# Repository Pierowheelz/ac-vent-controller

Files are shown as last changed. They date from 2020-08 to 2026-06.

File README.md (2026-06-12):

# Ducted Air Conditioner Vent Controller
This project uses an ESP32-based controller, stepper motors, TMC2209 (or similar) drivers and endstop switches (from a 3d printer kit) to control the circular Air Conditioner vents used in many ducted HVAC systems.
Each board can control up to 4 vents (leave the stepper header empty and tweak the /AC_Vent/config.h to control fewer vents). Multiple boards can be utilised to control more vents, or for vents too far from one board.

# Home Automation
This project is part of a larger ecosystem, designed to enable automation of vents based on the room temperatures, along with an App for manual control.
* [home-app-backend](https://github.com/Pierowheelz/home-app-backend) - backend API and automation logic
* [home-control](https://github.com/Pierowheelz/home-control) - web app for manual control

## Parts Required
* ESP32 Dev Board (NodeMCU-ESP32 DEVKITV1 - 30 pins - based on ESP-WROOM-32)
* 3D Printer Kit (from ebay or Aliexpress)
    * 4x Nema 17 stepper motors + cables
    * 4x Nema 17 mounting brackets
    * 4x Stepper motors drivers - A4988 or DRV8825 or TMC2208 (for quieter operation)
    * 4x RAMPS 1.4 switch endstops + cables (Note, swap the trigger switch for a waterproof one for more reliable operation, but keep the switch PCB)
* Order the PCB from the Gerber files (or custom-build with Perfboard 24 x 18 pins)
* 4x 150mm Lead screws + copper nuts (4mm pitch ideal, but any will work)
* DC-DC Buck convertor TRS2433 (or you can use an LM2596 set to 3.3v if DIYing the board)
* DC power supply (8-35 V)
* (optional) header-pin sockets for ESP32 and Stepper Drivers to allow quick removal/replacement
* A handfull of M4 screws & nuts
* Duct tape

## Process
1. Order the custom PCM from the Gerber files in the Circuit Board V2/ directory.
1. Print 4x Motor Bracket, Motor Cover, Endstop Clip in PLA or PETG (or other hard-plastic).
1. Print 4x Coupler, Damper and 8x End Holder in TPU (for vibration damping - PLA will work in a pinch though). Metal couplers from a 3d printer kit can also be used.
1. Assemble the circuitboard per the KiCad schematic or using the silk screen guides.
1. Set the ventNames, microStepping, WiFi parameters in the firmware (see AC_Vent/README_CONFIG.md for details).
1. Compile and flash the firmware onto your ESP32 dev board using Arduino IDE.
    * Using USB for power (do not plug in the power supply for this).
    * NOTE: Setup Arduino IDE with ESP32 library like this: https://randomnerdtutorials.com/installing-the-esp32-board-in-arduino-ide-windows-instructions/
1. Bench test by connecting motors and endstop switches.
    * You may need to switch the red and black wires on your endstop switches (black should be at the edge of the board, and red in the middle).
1. Connect the power supply to the high-voltage side of the buck convertor. This will power up the ESP32.
1. Tune the stepper motor current limit (Try this guide: https://www.makerguides.com/a4988-stepper-motor-driver-arduino-tutorial/).
    * Using USB for power (do not plug in the power supply for this).
1. On a computer, navigate to the IP Address of the device.
1. Click to open one of the Vents.
    * It will first spin counter-clockwise to close the vent until the endstop switch is triggered, then clockwise until the limit position is reached.
	* Note: If the motor spins the wrong direction, simply unplug and reverse it's connector.
1. Assemble components and install into vents. Tip: use Ethernet cable to extend leads as neccessary (I used RJ45 breakout modules but you could crimp connectors).

Note: There is no security or authentication in this system. Do not open up the port in your Router! For use on your internal network only.

## Usage via Rest API
Get vents status: `GET http://192.168.2.110/?&t=1`

Sample return:
```
{
	"0": {
		"name": "Room #1",
		"pos": 30
	},
	"1": {
		"name": "Room #2",
		"pos": 60
	},
	"2": {
		"name": "Room #3",
		"pos": 100
	}
}
```

Open vent `#1` to 100%: `GET http://192.168.2.110/?a=6&t=1&m=0&d=100`
Here `a` is the operating mode, where mode 6 corresponds to: open to ratio set by &d= (eg. ?d=050:open50%, ?d=000:close, ?d=100:open100%).
Also, `t` is the response type (1 = JSON).
And, `m` is the motor number (0-2).

The return format is identical to the 'get status' request.

## Images
Note: Some photos are from the prototype.

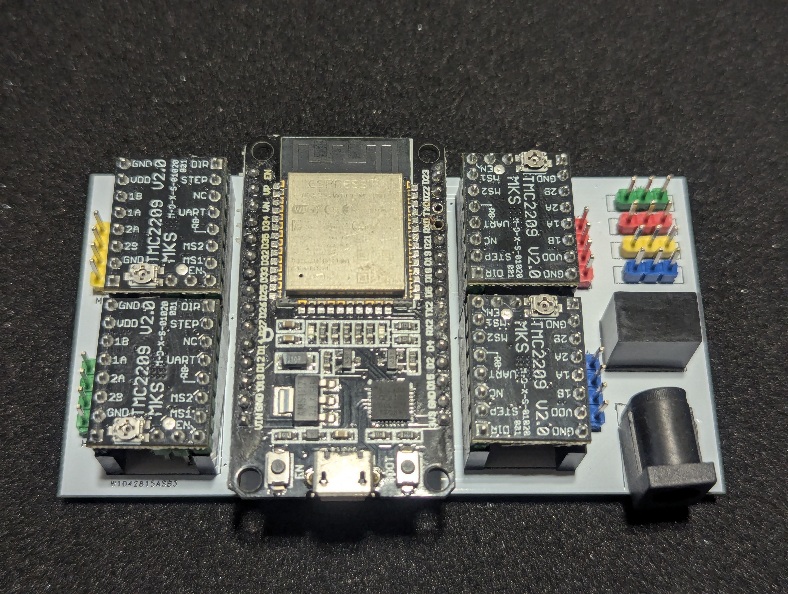
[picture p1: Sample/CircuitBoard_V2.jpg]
CircuitBoard_V2


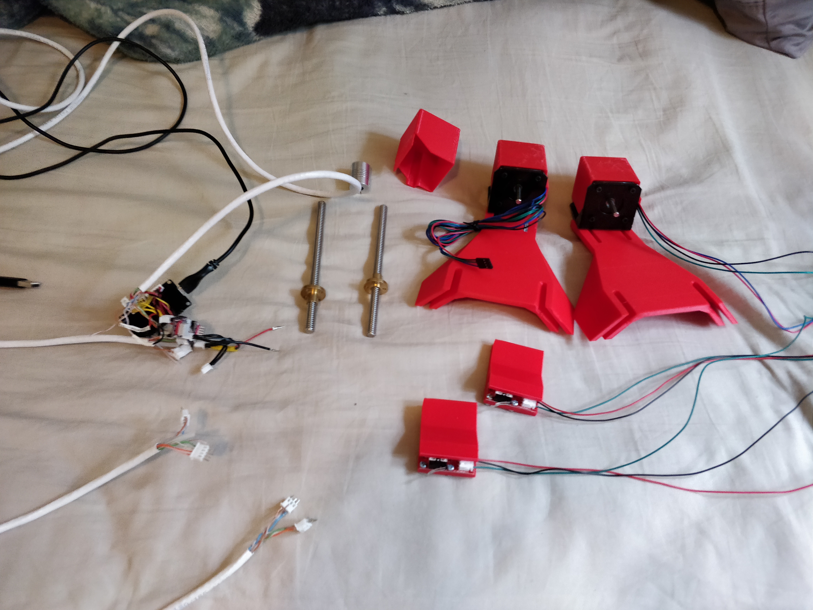
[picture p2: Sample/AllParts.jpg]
AllParts


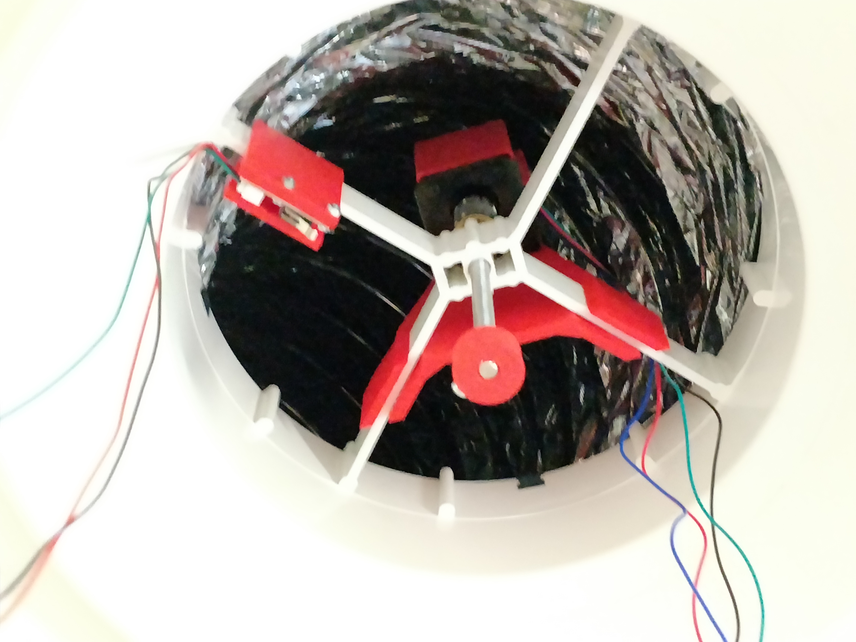
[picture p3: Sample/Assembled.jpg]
Assembled


BoartTop

BoardRear

BoardAssembled

BoardAssembled2

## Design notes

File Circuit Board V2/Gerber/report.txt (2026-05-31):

Plotted to '/home/peter/Apps/ac-vent-controller/Circuit Board V2/Gerber/Circuit Board V2-F_Cu.gtl'.
Plotted to '/home/peter/Apps/ac-vent-controller/Circuit Board V2/Gerber/Circuit Board V2-B_Cu.gbl'.
Plotted to '/home/peter/Apps/ac-vent-controller/Circuit Board V2/Gerber/Circuit Board V2-F_Paste.gtp'.
Plotted to '/home/peter/Apps/ac-vent-controller/Circuit Board V2/Gerber/Circuit Board V2-B_Paste.gbp'.
Plotted to '/home/peter/Apps/ac-vent-controller/Circuit Board V2/Gerber/Circuit Board V2-F_Silkscreen.gto'.
Plotted to '/home/peter/Apps/ac-vent-controller/Circuit Board V2/Gerber/Circuit Board V2-B_Silkscreen.gbo'.
Plotted to '/home/peter/Apps/ac-vent-controller/Circuit Board V2/Gerber/Circuit Board V2-F_Mask.gts'.
Plotted to '/home/peter/Apps/ac-vent-controller/Circuit Board V2/Gerber/Circuit Board V2-B_Mask.gbs'.
Plotted to '/home/peter/Apps/ac-vent-controller/Circuit Board V2/Gerber/Circuit Board V2-Edge_Cuts.gm1'.
Info: Done.

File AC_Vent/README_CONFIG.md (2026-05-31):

# AC Vent Controller Configuration

This project uses a separate configuration file to keep sensitive information out of version control.

## Setup Instructions

1. **Copy the sample configuration:**
   ```bash
   cp config_sample.h config.h
   ```

2. **Edit `config.h` with your actual values:**
   - WiFi SSID and password
   - Room names
   - IP addresses
   - Pin assignments (if different from default)
   - Motor settings

3. **Upload to your ESP32 as usual**

## Important Security Notes

- **`config.h` is ignored by git** and contains sensitive information
- **Never commit `config.h`** to version control
- **`config_sample.h`** is a template that can be committed safely
- Share `config_sample.h` with others but keep your `config.h` private

## Configuration Variables

- `NUM_MOTORS`: Number of vent motors (default: 4)
- `dirPins[]`: Direction control pins for each motor
- `stepper[]`: Step control pins for each motor
- `stepperPower[]`: Power control pins for each motor
- `endStop[]`: Endstop sensor pins for each motor
- `ventNames[]`: Display names for each vent/room
- `microStepping`: Microstepping setting (default: 8)
- `fullyOpen`: Steps for full vent opening (default: 1000)
- `stepDelay`: Delay between steps in microseconds (default: 2000)
- WiFi settings: SSID, password, and IP configuration

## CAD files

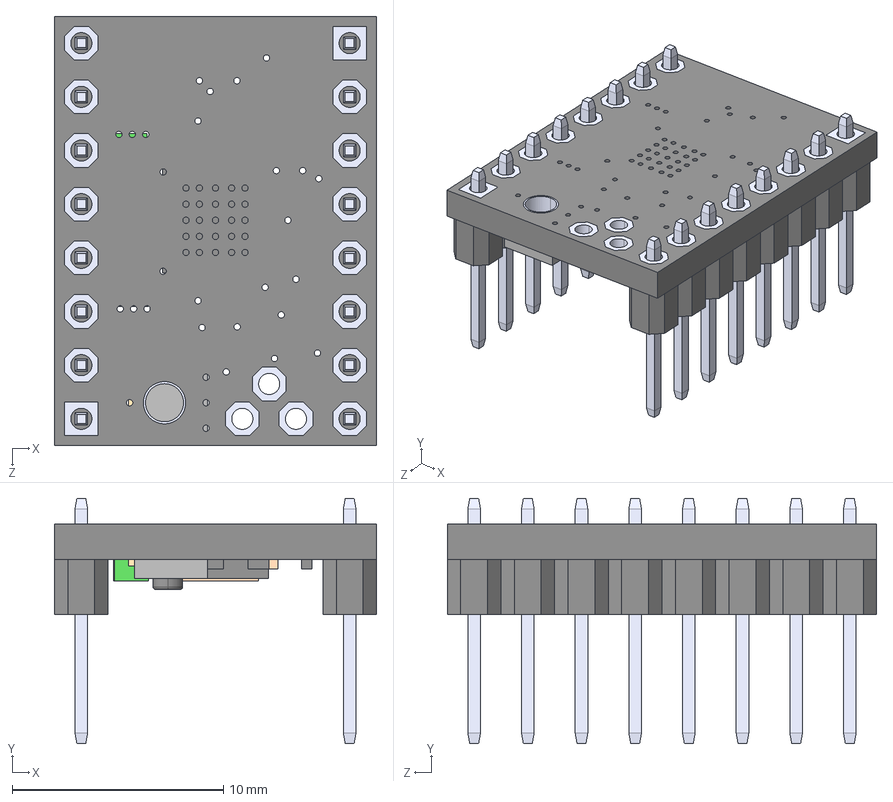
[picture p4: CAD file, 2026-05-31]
Circuit Board V2/ESP32/TMC2209_SILENTSTEPSTICK.step
15.2 x 11.6 x 20.3 mm

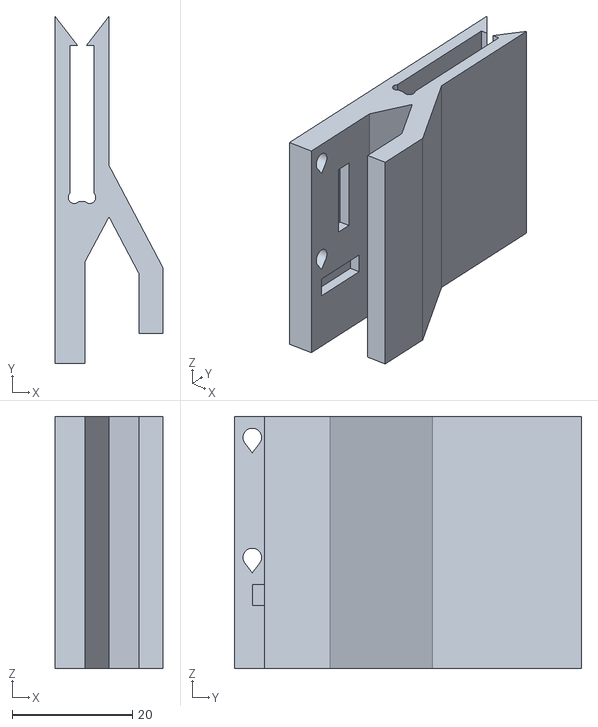
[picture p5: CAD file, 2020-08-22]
Parts/endstop-clip.stl
18.0 x 57.9 x 42.0

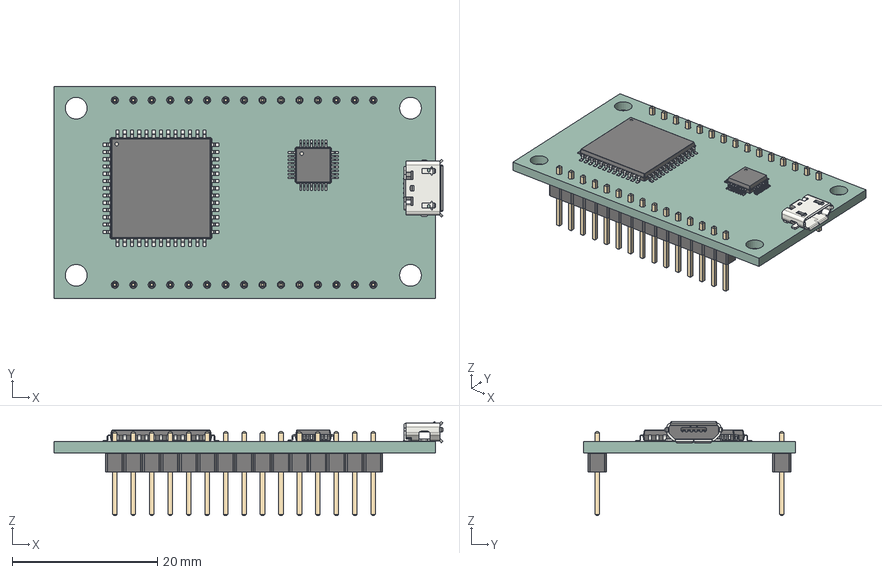
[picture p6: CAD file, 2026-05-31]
Circuit Board V2/ESP32/ESP32-30pin.step
53.5 x 29.2 x 12.9 mm
LQFP_52_14x14mm_P1mm
USB_Micro-B_Molex_47346-0001
LQFP_32_5x5mm_P05mm
PinHeader_1x15_P254mm_Vertical x 2
ESP32-30pin PCB

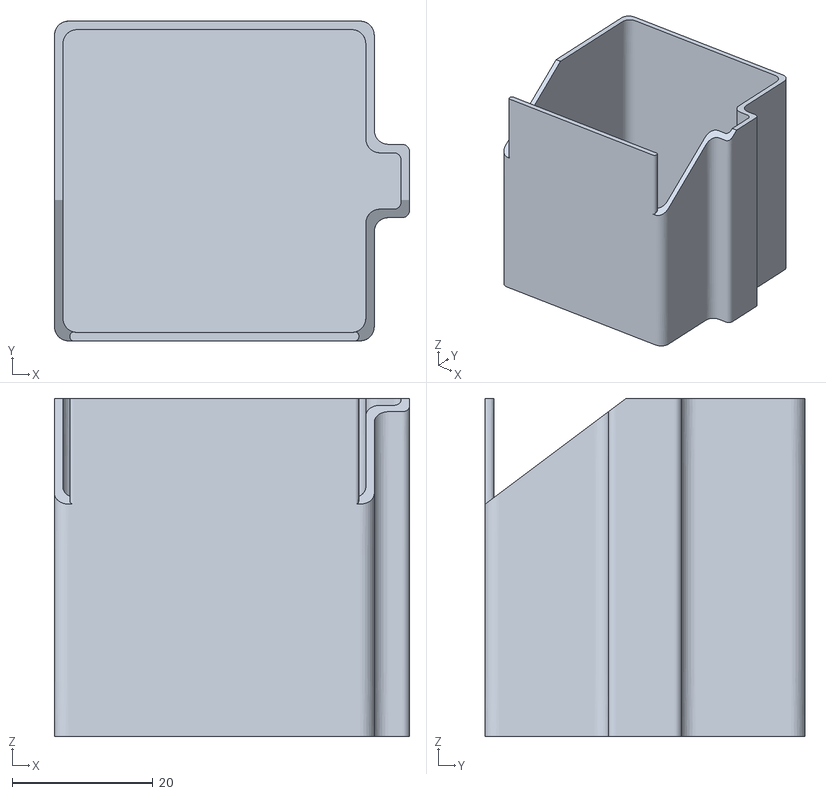
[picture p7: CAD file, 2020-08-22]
Parts/motor-cover.stl
50.4 x 45.4 x 48.0

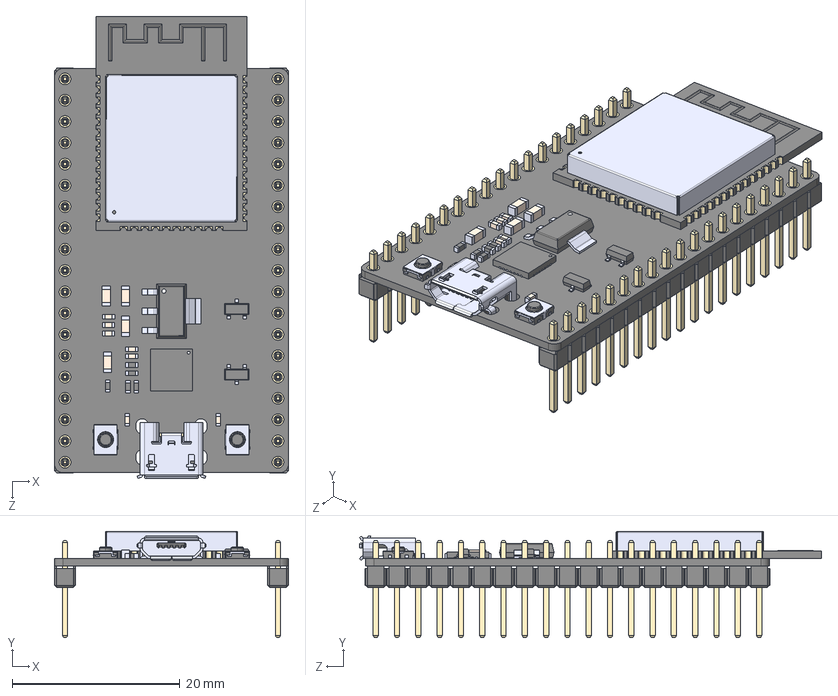
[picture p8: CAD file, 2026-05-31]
Circuit Board V2/ESP32/DEVKIT_V1_ESP32-WROOM-32.step
27.9 x 12.7 x 55.1 mm
board
header x 2
ESP32-WROOM-32D
micro usb
button x 2
CP2102N-A01-GQFN28
AMS1117-3.3
SS8050-G
components^DEVKIT V1 ESP32-WROOM-32

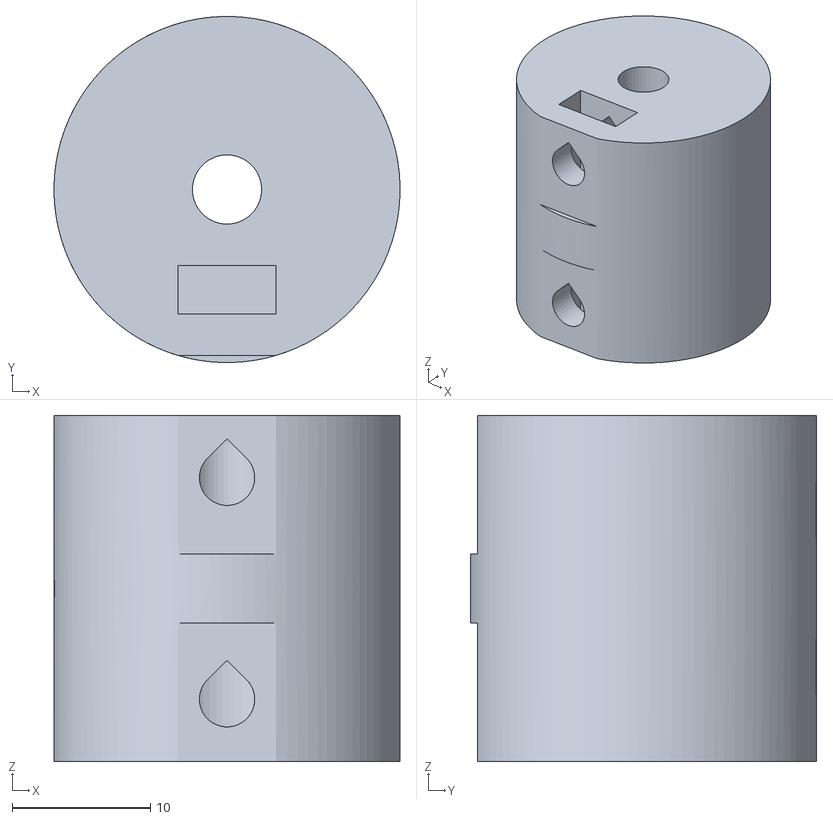
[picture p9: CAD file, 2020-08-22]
Parts/coupler.stl
25.0 x 25.0 x 25.0

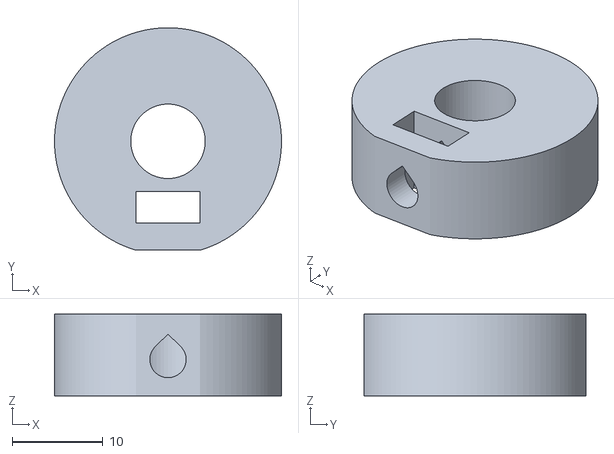
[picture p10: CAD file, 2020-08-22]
Parts/end-holder.stl
25.0 x 24.5 x 9.00

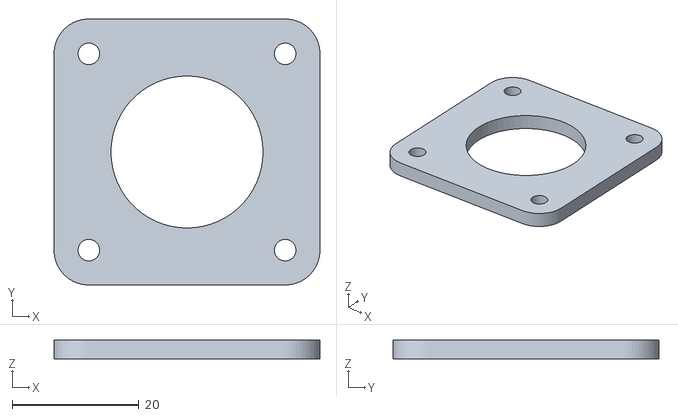
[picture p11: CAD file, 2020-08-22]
Parts/damper.stl
42.0 x 42.0 x 3.00

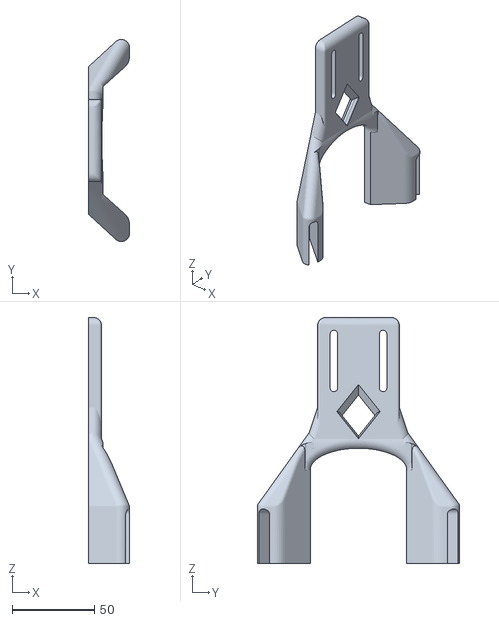
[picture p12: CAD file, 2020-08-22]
Parts/motor-bracket.stl
25.0 x 123.2 x 150.0

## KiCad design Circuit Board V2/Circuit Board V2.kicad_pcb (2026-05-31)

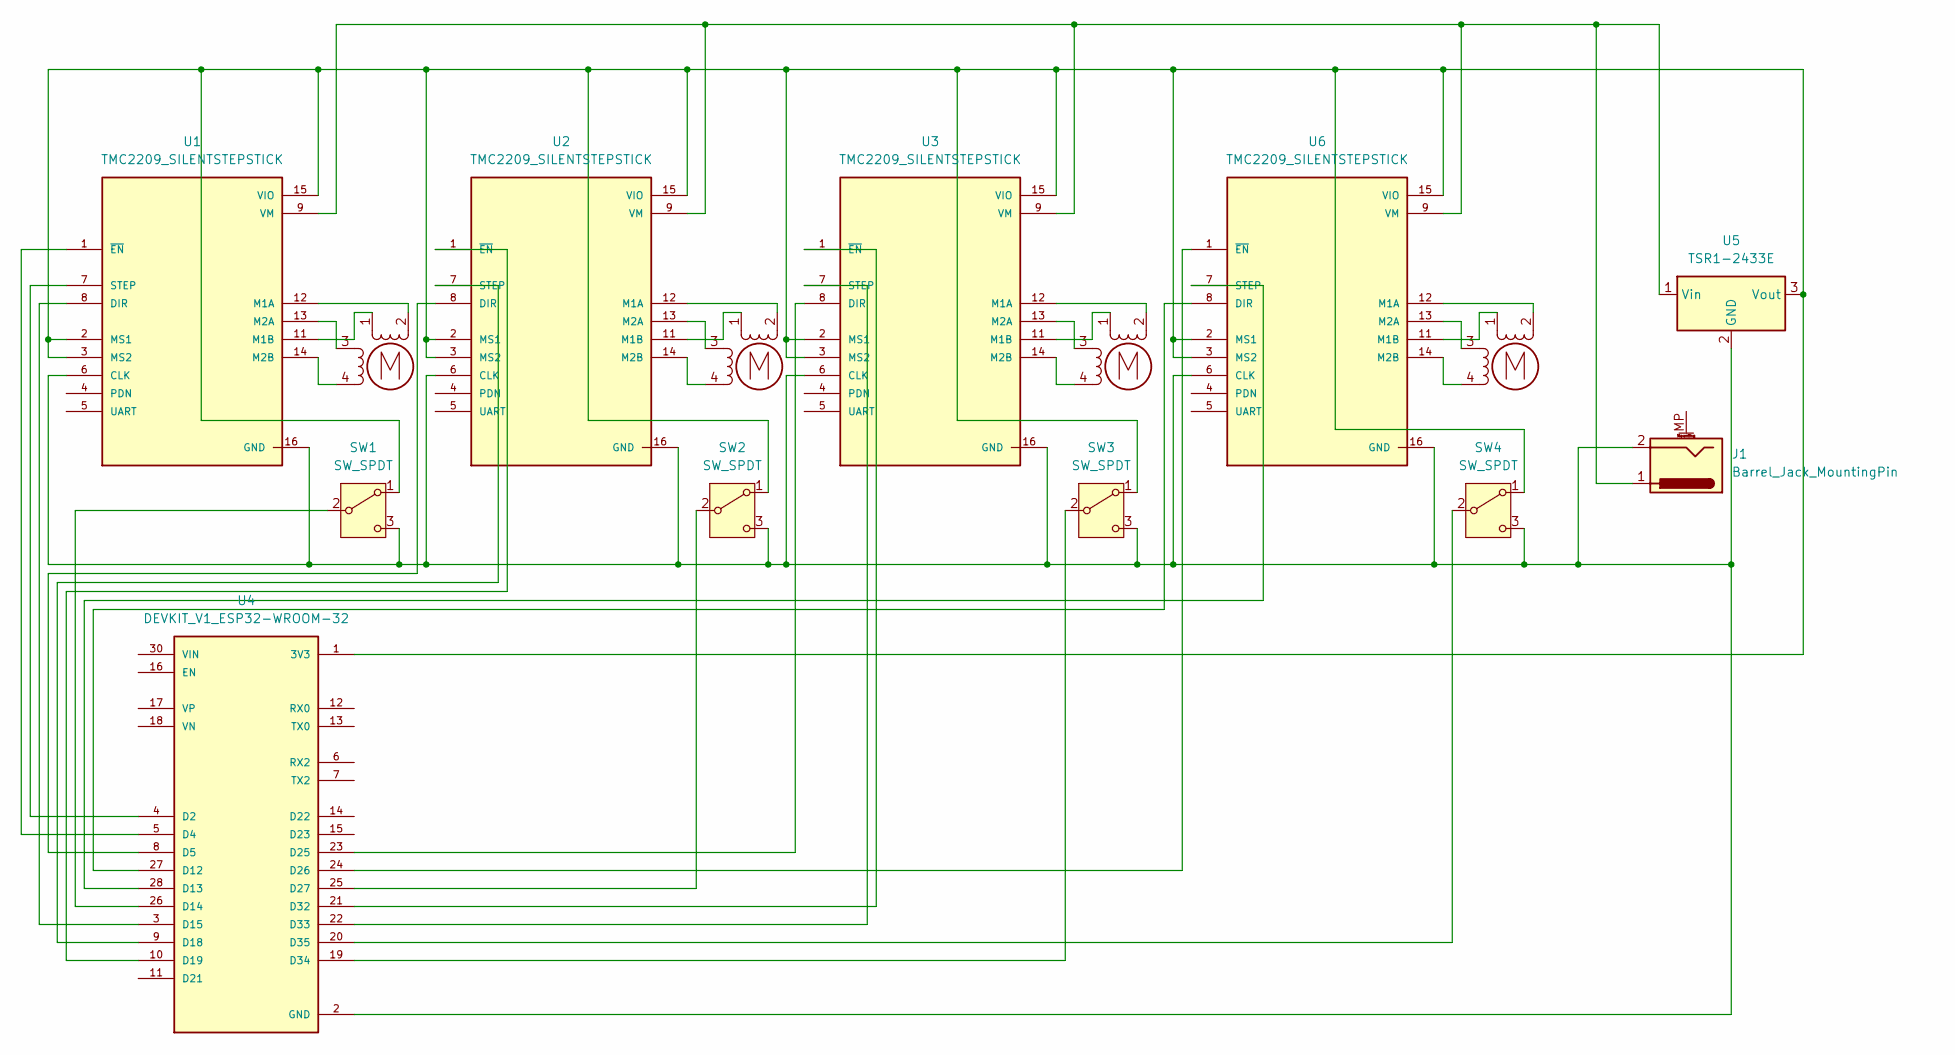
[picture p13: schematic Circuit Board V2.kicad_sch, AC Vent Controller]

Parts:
J1: Barrel_Jack_MountingPin; BarrelJack_Horizontal
M1, M2, M3, M4: Stepper_Motor_bipolar; PinHeader_1x04_P2.54mm_Vertical
SW1, SW2, SW3, SW4: SW_SPDT; SW_Slide-03_Wuerth-WS-SLTV_10x2.5x6.4_P2.54mm
U1, U2, U3, U6: TMC2209_SILENTSTEPSTICK; MODULE_TMC2209_SILENTSTEPSTICK; PARTREV 1.20
U4: DEVKIT_V1_ESP32-WROOM-32; MODULE_DEVKIT_V1_ESP32-WROOM-32
U5: TSR1-2433E; Converter_DCDC_TRACO_TSR1-xxxxE_THT

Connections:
GND: J1.2, SW1.3 (C), SW2.3 (C), SW3.3 (C), SW4.3 (C), U1.6 (CLK), U1.10 (GND), U1.16 (GND), U2.6 (CLK), U2.10 (GND), U2.16 (GND), U3.6 (CLK), U3.10 (GND), U3.16 (GND), U4.2 (GND), U4.29 (GND), U5.2 (GND), U6.6 (CLK), U6.10 (GND), U6.16 (GND)
unnamed: M1.2 (-_2), U1.12 (M1A)
unnamed: M2.2 (-_2), U2.12 (M1A)
unnamed: M3.2 (-_2), U3.12 (M1A)
unnamed: M4.2 (-_2), U6.12 (M1A)
unnamed: SW1.1 (A), SW2.1 (A), SW3.1 (A), SW4.1 (A), U1.2 (MS1), U1.3 (MS2), U1.15 (VIO), U2.2 (MS1), U2.3 (MS2), U2.15 (VIO), U3.2 (MS1), U3.3 (MS2), U3.15 (VIO), U4.1 (3V3), U5.3 (Vout), U6.2 (MS1), U6.3 (MS2), U6.15 (VIO)
unnamed: SW1.2 (B), U4.26 (D14)
unnamed: SW2.2 (B), U4.25 (D27)
unnamed: SW3.2 (B), U4.19 (D34)
unnamed: SW4.2 (B), U4.20 (D35)
unnamed: U1.8 (DIR), U4.3 (D15)
unnamed: M1.1, U1.11 (M1B)
unnamed: M1.3, U1.13 (M2A)
unnamed: M1.4, U1.14 (M2B)
unnamed: U1.7 (STEP), U4.4 (D2)
unnamed: J1.1, U1.9 (VM), U2.9 (VM), U3.9 (VM), U5.1 (Vin), U6.9 (VM)
unnamed: U1.1 (~EN), U4.5 (D4)
unnamed: U2.8 (DIR), U4.8 (D5)
unnamed: M2.1, U2.11 (M1B)
unnamed: M2.3, U2.13 (M2A)
unnamed: M2.4, U2.14 (M2B)
unnamed: U2.7 (STEP), U4.9 (D18)
unnamed: U2.1 (~EN), U4.10 (D19)
unnamed: U3.8 (DIR), U4.23 (D25)
unnamed: M3.1, U3.11 (M1B)
unnamed: M3.3, U3.13 (M2A)
unnamed: M3.4, U3.14 (M2B)
unnamed: U3.7 (STEP), U4.22 (D33)
unnamed: U3.1 (~EN), U4.21 (D32)
unnamed: U4.27 (D12), U6.8 (DIR)
unnamed: U4.28 (D13), U6.7 (STEP)
unnamed: U4.24 (D26), U6.1 (~EN)
unnamed: M4.1, U6.11 (M1B)
unnamed: M4.3, U6.13 (M2A)
unnamed: M4.4, U6.14 (M2B)

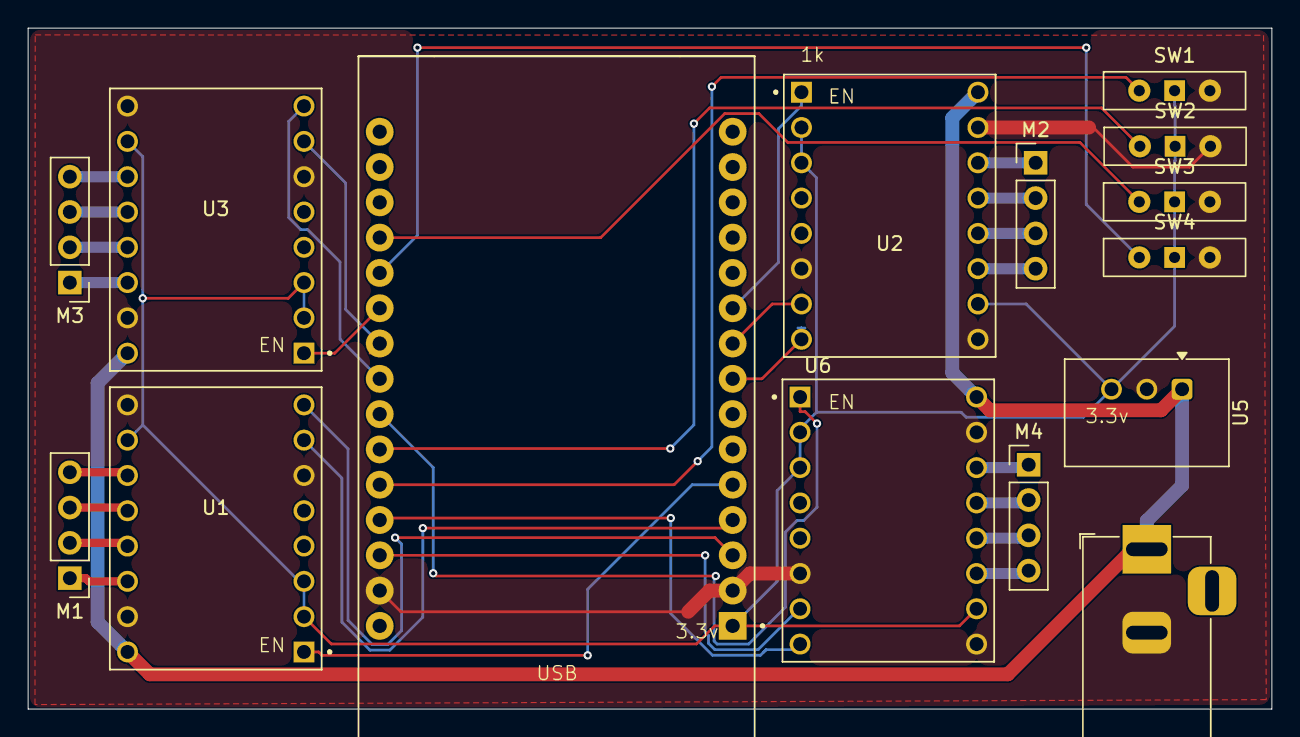
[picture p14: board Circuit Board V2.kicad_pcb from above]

Board: 2 copper layers, 89.5 x 49.0 mm, 15 parts (0 on the bottom side), 35 nets.

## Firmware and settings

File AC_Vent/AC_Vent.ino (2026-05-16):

/*
 *
 #ESP32 controller for AC Vents
 Peter Wells - March 2020

Version 1.7.0
 Moved motor controls to a second FreeRTOS thread (Core 0)
 Requests return instantly, reporting target position
 Added ability to set fully open position per-motor
 More resilient phantom endstop detection

Version 1.6.0
 Added acceleration ramping to the motor

 Version 1.5.0
  Moved configuration to config.h
  Added WiFi connection management

 Version 1.4.0
  Startup state determined by endstop status (rather than EEPROM)

 Version 1.3.0
  Added simple JSON API

 Version 1.2.0
  Support microstepping

 Version 1.1.0
  Added debouncing
  Swap buttons with Javascript for <a href... for IOS support
  
 Version 1.0.0
  Initial version
*/
#include <WiFi.h>
#include <esp_task_wdt.h>
#include "config.h"

// Configuration variables are now loaded from config.h
// Copy config_sample.h to config.h and update with your actual values

// Motor trigger values (invert if motor spins the wrong direction)
const int openVent = LOW;
const int closeVent = HIGH;

volatile int stepperPos[NUM_MOTORS];      // Current actual position (updated by motor task)
volatile int targetPos[NUM_MOTORS];       // Target position (set by request handler)
volatile bool closeRequested[NUM_MOTORS]; // True when close-to-endstop is requested
volatile bool motorBusy[NUM_MOTORS];      // True while a motor is actively moving
/** Set true when a raw endstop press is seen before checkEndstopStatus() confirms (phantom path). */
volatile bool endstopTriggerPending[NUM_MOTORS];
/** Microstepping-compensated full-open position per motor (steps). Filled in setup() from fullyOpen[] */
int fullyOpenMicro[NUM_MOTORS];
int stpDelay = stepDelay / microStepping; //set delay compensating for MicroStepping

WiFiServer server(80);
TaskHandle_t motorTaskHandle = NULL;

//function defaults
void spinMotor( int motor=0, int dir=LOW, int dist=1 );
void findZero( int motor=0, int dir=LOW );
void ensureOpen( int closeMotor=0, int openStatus=0 );
void checkWiFiConnection();
void motorTask( void* parameter );
void serviceWatchdogAndYield( int stepCounter );
bool checkEndstopStatus( int motor );
//end function defaults

/**
 * @brief True if the closed endstop reads pressed (active LOW).
 * @param motor Motor index in endStop[].
 */
static bool endstopPressed(int motor) {
  return digitalRead(endStop[motor]) == LOW;
}

/**
 * @brief True when homing may continue stepping along the current segment.
 *
 * When homingPressEvents is null: raw pin HIGH means released.
 * When homingPressEvents is non-null (findZero): updates endstopTriggerPending and
 * homingPressEvents for phantom deferral — returns true while the pin is HIGH, or
 * while a LOW read is not yet confirmed by checkEndstopStatus(). Returns false only
 * when checkEndstopStatus() confirms the endstop (stop homing). On HIGH, clears
 * pending and resets homingPressEvents.
 *
 * @param motor              Motor index in endStop[].
 * @param homingPressEvents  Optional; when set, findZero phantom / confirm logic applies.
 * @return False only when the endstop is debounce-confirmed; otherwise keep stepping.
 */
static bool endstopReleased(int motor, int* homingPressEvents = nullptr) {
  const bool pinHigh = digitalRead(endStop[motor]) == HIGH;

  if (homingPressEvents == nullptr) {
    return pinHigh;
  }

  if (pinHigh) {
    endstopTriggerPending[motor] = false;
    *homingPressEvents = 0;
    return true;
  }

  endstopTriggerPending[motor] = true;
  *homingPressEvents += 1;

  if (*homingPressEvents < ENDSTOP_PHANTOM_CONFIRM_TRIGGERS) {
    return true;
  }

  if (checkEndstopStatus( motor )) {
    endstopTriggerPending[motor] = false;
    return false;
  }

  Serial.println("Phantom trigger detected - continuing...");
  *homingPressEvents = 0;
  return true;
}

/** Delay between endstop validation samples (milliseconds). */
static const int ENDSTOP_SAMPLE_DELAY_MS = 2;
/** Number of endstop validation samples taken per check. */
static const int ENDSTOP_SAMPLE_COUNT = 10;
/** Minimum pressed samples required to confirm a trigger. */
static const int ENDSTOP_PRESSED_THRESHOLD = 7;

// Check and maintain WiFi connection
void checkWiFiConnection() {
  if (WiFi.status() != WL_CONNECTED) {
    Serial.println("WiFi connection lost. Attempting to reconnect...");
    WiFi.disconnect();
    delay(1000);

    if (!WiFi.config(local_IP, gateway, subnet, primaryDNS, secondaryDNS)) {
      Serial.println("STA Failed to configure");
    }

    WiFi.begin(ssid, password);

    unsigned long wifiStartTime = millis();
    const unsigned long WIFI_TIMEOUT = 10000; // 10 second timeout

    while (WiFi.status() != WL_CONNECTED && (millis() - wifiStartTime) < WIFI_TIMEOUT) {
      delay(500);
      Serial.print(".");
    }

    if (WiFi.status() == WL_CONNECTED) {
      Serial.println("");
      Serial.println("WiFi reconnected!");
      Serial.println("IP address: ");
      Serial.println(WiFi.localIP());
    } else {
      Serial.println("");
      Serial.println("WiFi reconnection failed!");
    }
  }
}

void setup()
{
  Serial.begin(115200);
  // initialize EEPROM with predefined size (for power outage recovery of position)
  // EEPROM.begin(NUM_MOTORS);
  
  for (int i=0; i < NUM_MOTORS; i++){
    fullyOpenMicro[i] = fullyOpen[i] * microStepping;
    //setup pin modes for each motor
    pinMode(dirPins[i], OUTPUT);      // set stepper pin mode
    pinMode(stepper[i], OUTPUT);      // set stepper pin mode
    pinMode(stepperPower[i], OUTPUT);      // set stepperPower pin mode
    digitalWrite(stepperPower[i], HIGH);
    pinMode(endStop[i], INPUT_PULLUP);      // endstops are active LOW; pull-up prevents floating inputs

    // Setup initial Stepper Pos to either 0 or 100% based on whether endstop is triggered
    stepperPos[i] = fullyOpenMicro[i]; // Default to vent open
    if( checkEndstopStatus( i ) ){
      stepperPos[i] = 0; // Vent is closed
    }

    targetPos[i] = stepperPos[i];
    closeRequested[i] = false;
    motorBusy[i] = false;
   
  } //end for loop

  // We start by connecting to a WiFi network
  Serial.println();
  Serial.println("Starting WiFi ");
  if (!WiFi.config(local_IP, gateway, subnet, primaryDNS, secondaryDNS)) {
      Serial.println("STA Failed to configure");
  }
  
  Serial.print("Connecting to ");
  Serial.println(ssid);

  WiFi.begin(ssid, password);

  while (WiFi.status() != WL_CONNECTED) {
      delay(500);
      Serial.print(".");
  }
  Serial.println("");
  Serial.println("WiFi connected! ");
  Serial.println("IP address: ");
  Serial.println(WiFi.localIP());
  Serial.print("ESP Mac Address: ");
  Serial.println(WiFi.macAddress());
  
  server.begin();

  xTaskCreatePinnedToCore(
    motorTask,
    "MotorTask",
    4096,
    NULL,
    1,
    &motorTaskHandle,
    0  // Core 0 (loop runs on Core 1)
  );
}

void loop(){
  checkWiFiConnection();  // Check and maintain WiFi connection

  WiFiClient client = server.available();      // listen for incoming clients

  if (client) {
    String currentLine = "";                   // make a String to hold incoming data from the client
    int respType = 0; // 0=html, 1=json
    unsigned long requestStartTime = millis(); // Add timeout tracking
    const unsigned long REQUEST_TIMEOUT = 5000; // 5 second timeout
    bool requestProcessed = false;
    const int MAX_LINE_LENGTH = 2048; // Prevent memory exhaustion

    while (client.connected() && !requestProcessed && (millis() - requestStartTime) < REQUEST_TIMEOUT) {
      if (client.available()) {                // if there's client data
        char c = client.read();                // read a byte
        if( c == '\r' && currentLine.startsWith("GET /") ){
          // Check to see if the client request was "GET /H" or "GET /L":
          
          // Basic request validation
          if (!currentLine.startsWith("GET /")) {
            Serial.println("Invalid request format");
            client.stop();
            return;
          }

          int typePos = currentLine.indexOf("&t="); // 1-digit
          if( typePos > 0 ){
            respType = currentLine.substring( typePos+3, typePos+4 ).toInt(); // type=1 means JSON response
          }

          int actionPos = currentLine.indexOf("?a="); // 1-digit
          if( actionPos > 0 ){
            int action = currentLine.substring( actionPos+3, actionPos+4 ).toInt();

            // Validate action is within valid range
            if (action < 0 || action > 6) {
              Serial.println("Invalid action parameter");
              client.stop();
              return;
            }

            int dist = 0;
            int distPos = currentLine.indexOf("&d="); // 3-digits (eg. 050)
            if( distPos > 0 ){
              dist = currentLine.substring( distPos+3, distPos+6 ).toInt();
            }
            int distAmount = dist * 100;

            int motorNum = 0;
            int motorPos = currentLine.indexOf("&m="); // 1-digit
            if( motorPos > 0 ){
              motorNum = currentLine.substring( motorPos+3, motorPos+4 ).toInt();
            }

            // Validate motor number is within valid range
            if (motorNum < 0 || motorNum >= NUM_MOTORS) {
              Serial.println("Invalid motor number");
              client.stop();
              return;
            }
            
            Serial.print("Action: ");
            Serial.println(action);
            Serial.print("Dist: ");
            Serial.println(dist);
            switch( action ){
              case 0: //TEST - spin anti-clockwise
                targetPos[motorNum] = stepperPos[motorNum] + distAmount;
                break;
              case 1: //TEST - spin clockwise
                targetPos[motorNum] = stepperPos[motorNum] - distAmount;
                break;
              case 2: //close completely (zero)
                closeRequested[motorNum] = true;
                targetPos[motorNum] = 0;
                break;
              case 3: //open completely
                targetPos[motorNum] = fullyOpenMicro[motorNum];
                break;
              case 4: //open 50%
                targetPos[motorNum] = fullyOpenMicro[motorNum] / 2;
                break;
              case 5: //open 25%
                targetPos[motorNum] = fullyOpenMicro[motorNum] / 4;
                break;
              case 6: //open to ratio set by &d= (eg. ?d=050:open50%, ?d=000:close, ?d=100:open100%)
                targetPos[motorNum] = (fullyOpenMicro[motorNum] / 100) * dist;
                if (targetPos[motorNum] == 0) {
                  closeRequested[motorNum] = true;
                }
           
                break;
            }
          }
      } else if (c == '\n') {                  // check for newline character,
          if (currentLine.length() == 0) {     // if line is blank it means its the end of the client HTTP request
            int pos[NUM_MOTORS];
            if( respType == 0 ){
                Serial.println("Sending HTML response.");
                // HTML response
                client.println("<!DOCTYPE html>"); // open wrap the web page
                client.print("<html><head>");
                client.print("<meta charset='utf-8'>");
                client.print("<meta name='viewport' content='initial-scale=1.0'>");
                client.print("<link rel='shortcut icon' href='https://webbird.net.au/peter/vent_icon.ico'>");
                client.print("<link rel='icon' sizes='256x256' href='https://webbird.net.au/peter/vent_icon.png'>");
                client.print("<link rel='apple-touch-icon-precomposed' sizes='256x256' href='https://webbird.net.au/peter/vent_icon.png'>");
                client.print("<link rel='manifest' href='https://webbird.net.au/peter/vent_manifest.json'>");
                client.print("<meta name='apple-mobile-web-app-capable' content='yes'>");
                client.print("<meta name='mobile-web-app-capable' content='yes'>");
                client.print("<meta name='viewport' content='initial-scale=1.0'>");
                client.print("<title>AC Vent Controls</title>");
                client.print("<style>");
                client.print( "html, body{height:100%;overflow:hidden;margin:0;padding:5px;text-align:center;background:#333333;font-family:sans-serif;}");
                client.print( "h1,h4,a{text-transform:uppercase;color:#DADADA;}");
                client.print( "a{text-decoration:none;}");
                client.print( ".button_row{display:flex;align-items:center;}");
                client.print( ".button{flex-grow:1;flex-basis:1;padding:12px 2px;background:#202021;border:1px solid #5C5C5C;color:#DADADA;margin:0 4px; text-transform:uppercase;cursor:pointer;}");
                client.print( ".status_row{width:100%;height:30px;margin:8px 4px;position:relative;background:#202021;border:1px solid #5C5C5C;}");
                client.print( ".statusbar{width:0%;height:100%;position:absolute;top:0;left:0;background:#18BAC8;transition:width 1s ease;}");
                client.print("</style>");
                client.print("<script type='text/javascript'>");
                client.print( "history.replaceState({}, 'AC Vent Controls', '/');");
                client.print("</script>");
                client.print("</head>");
                client.print("<body><h1><a href=\"/\">AC Vent Controls</a></h1>");
                // Gui buttons start here
                for (int i=0; i < NUM_MOTORS; i++){
                  pos[i] = 0;
                  if( targetPos[i] > 0 ){
                    Serial.println("Calculating position...");
                    Serial.print("TargetPos: ");
                    Serial.println(targetPos[i]);
                    Serial.print("EndPos: ");
                    Serial.println(fullyOpenMicro[i]);
                    Serial.print("Ratio: ");
                    float ratio = targetPos[i] / float(fullyOpenMicro[i]);
                    Serial.println(ratio);
                    pos[i] = ratio * 100;
                  }
                  client.print("<h4>");
                  client.print( ventNames[i]);
                  client.print("</h4>");
                  client.print("<div class='button_row'>");
                  client.print( "<a class='button' href='/?a=2&m=");
                  client.print(   i);
                  client.print( "'>Closed</a>");
                  client.print( "<a class='button' href='/?a=5&m=");
                  client.print(   i);
                  client.print( "'>25%</a>");
                  client.print( "<a class='button' href='/?a=4&m=");
                  client.print(   i);
                  client.print( "'>50%</a>");
                  client.print( "<a class='button' href='/?a=3&m=");
                  client.print(   i);
                  client.print( "'>Open</a>");
                  client.print("</div>");
                  client.print("<div class='status_row'>");
                  client.print( "<div class='statusbar' style='width:");
                  client.print(   pos[i]);
                  client.print( "%'></div>");
                  client.print("</div>");

                  Serial.print("Position: ");
                  Serial.println(pos[i]);
                }
                client.print("</body></html>"); // close wrap the web page
            } else {
                Serial.println("Sending JSON response.");
                // JSON response - eg. {"0":{"name":"Vent #1","pos":50},"1":...}
                client.println("HTTP/1.1 200 OK");
                client.println("Content-Type: application/json;charset=utf-8");
                client.println("Server: Arduino");
                client.println("Connection: close");
                client.println();
                client.print("{");
                for (int i=0; i < NUM_MOTORS; i++){
                  pos[i] = 0;
                  if( targetPos[i] > 0 ){
                    Serial.println("Calculating position...");
                    Serial.print("TargetPos: ");
                    Serial.println(targetPos[i]);
                    Serial.print("EndPos: ");
                    Serial.println(fullyOpenMicro[i]);
                    Serial.print("Ratio: ");
                    float ratio = targetPos[i] / float(fullyOpenMicro[i]);
                    Serial.println(ratio);
                    pos[i] = ratio * 100;
                  }
                  // Print: "0":{"name":"Vent #1","pos":50,"busy":false},
                  client.print( "\"" );
                  client.print( i );
                  client.print( "\":{\"name\":\"" );
                  client.print( ventNames[i] );
                  client.print( "\",\"pos\":" );
                  client.print( pos[i] );
                  client.print( ",\"busy\":" );
                  client.print( motorBusy[i] ? "true" : "false" );
                  client.print( "}" );
                  if( i+1 < NUM_MOTORS ){ //add trailing comma to all but the last motor
                      client.print( "," );
                  }

                  Serial.print("Position: ");
                  Serial.println(pos[i]);
                }
                client.print("}");
            }
            
            client.println(); // The HTTP response ends with an extra blank line:

            requestProcessed = true; // Mark request as processed
            break;  // break out of the while loop:
          } else {    // if you got a newline, then clear currentLine:
            currentLine = "";
          }
        } else if (c != '\r') {  // if you got anything else but a carriage return character,
          if (currentLine.length() < MAX_LINE_LENGTH) {  // Prevent memory exhaustion
            currentLine += c;       // add it to the end of the currentLine
          } else {
            Serial.println("Request line too long - possible attack or malformed request");
            client.stop();
            return;
          }
        }
      }
    }

    // Handle timeout - close connection if request wasn't processed
    if (!requestProcessed && (millis() - requestStartTime) >= REQUEST_TIMEOUT) {
      Serial.println("Request timeout - closing connection");
      client.stop();
    }
  }
}

/**
 * @brief FreeRTOS task that drives motors toward their target positions.
 *
 * Runs on Core 0 in a continuous loop. For each motor it checks whether a
 * close-to-endstop was requested (closeRequested) or whether targetPos
 * differs from stepperPos, and performs the appropriate move. If an endstop
 * interrupts a positional move and no new target has been set, targetPos is
 * synced to the actual position to avoid retry loops.
 *
 * @param parameter Unused FreeRTOS task parameter.
 */
void motorTask( void* parameter ){
  esp_task_wdt_add(NULL);
  for(;;){
    esp_task_wdt_reset();
    for( int i = 0; i < NUM_MOTORS; i++ ){
      if( closeRequested[i] ){
        motorBusy[i] = true;
        closeRequested[i] = false;
        ensureOpen( i, 0 );
        findZero( i, closeVent );
        motorBusy[i] = false;
      } else if( targetPos[i] != stepperPos[i] ){
        motorBusy[i] = true;
        int target = targetPos[i];
        ensureOpen( i, target );
        moveMotorTo( i, target );
        // Sync target if endstop interrupted the move and no new target was set
        if( stepperPos[i] != target && targetPos[i] == target ){
          targetPos[i] = stepperPos[i];
        }
        motorBusy[i] = false;
      }
    }
    vTaskDelay(10 / portTICK_PERIOD_MS);
  }
}

/*
 * Move a motor to an absolute position (in microSteps)
 */
void moveMotorTo( int motor, int pos ){
  int motorPos = stepperPos[motor];
  
  Serial.print("Start Position: ");
  Serial.println(stepperPos[motor]);
  if( motorPos < 0 ){ //motor position unknown
    Serial.println("Zeroing");
    findZero( motor, closeVent );
    motorPos = 0;
  }

  int dist = pos - motorPos;
  int dir = openVent;
  if( dist < 0 ){
    dir = closeVent;
    dist = -dist;
  }

  Serial.print("Distance: ");
  Serial.println(dist);
  Serial.print("Direction: ");
  Serial.println(dir);

  spinMotor( motor, dir, dist );

  Serial.print("End Position: ");
  Serial.println(stepperPos[motor]);
}

/**
 * @brief Feed this task watchdog and briefly yield so IDLE tasks can run.
 *
 * @param stepCounter Current loop step index.
 */
void serviceWatchdogAndYield( int stepCounter ){
  if( stepCounter % 100 == 0 ){
    esp_task_wdt_reset();
    vTaskDelay(1 / portTICK_PERIOD_MS);
  }
}
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

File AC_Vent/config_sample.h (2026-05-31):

/*
 * Sample configuration file for AC Vent Controller
 * Copy this file to config.h and update with your actual values
 *
 * WARNING: config.h contains sensitive information and should NOT be committed to version control
 */

// ---------------------------------------------------------------------------------------------------------------------
// -- START USER CONFIGURATION --
// ---------------------------------------------------------------------------------------------------------------------

#define NUM_MOTORS 3

const int dirPins[] = { //Pins controlling direction of stepper
  15, //Room 1
  5,  //Room 2
  25, //Room 3
  12  //Room 4
};
const int stepper[] = { //Pins controlling stepper steps
  2,
  18,
  33,
  13
};
const int stepperPower[] = { //Pins controlling stepper power
  4,
  19,
  32,
  26
};
const int endStop[] = { // endstop switch pins (active LOW)
  14,
  27,
  34,
  35
};
const char* ventNames[] = { //Display names for each vent/room
  "Room 1",
  "Room 2",
  "Room 3",
  "Room 4"
};

// Current microstepping setting (no need to vary stepDelay); fullyOpen[] is per motor
const int microStepping = 16; //1=no microStepping, 32=max (on DRV8825)

// Full-open travel in full steps (200 per rotation), one entry per motor — multiplied by microStepping at runtime
const int fullyOpen[] = {
  1000,
  1000,
  1000
};
static_assert(sizeof(fullyOpen) / sizeof(fullyOpen[0]) == NUM_MOTORS,
              "fullyOpen[] must have NUM_MOTORS entries");

// Endstop phantom rejection: require this many separate approaches (press events) before
// running the blocking checkEndstopStatus() debounce (findZero homing and spinMotor close).
const int ENDSTOP_PHANTOM_CONFIRM_TRIGGERS = 2;

//Speed of the motor (in Microseconds)
const int stepDelay = 2000; //delay between steps (1000 = fastest, 5000 = pretty slow)

// Wifi / Network settings
const char* ssid    = "YOUR_WIFI_SSID";         // Your WiFi network name
const char* password = "YOUR_WIFI_PASSWORD";    // Your WiFi password

IPAddress local_IP(192, 168, 1, 100);      // Static IP for your ESP32
IPAddress gateway(192, 168, 1, 1);         // Your router's IP
IPAddress subnet(255, 255, 255, 0);       // Subnet mask
IPAddress primaryDNS(8, 8, 8, 8);         // Google DNS (optional)
IPAddress secondaryDNS(8, 8, 4, 4);       // Google DNS (optional)
// ---------------------------------------------------------------------------------------------------------------------
// -- END USER CONFIGURATION --
// ---------------------------------------------------------------------------------------------------------------------

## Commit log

2020-08-22 Initial git commit
    Added additional resources. Begun work on adding microstepping (incomplete). Non-functional build.
    [coupler.stl, damper.stl, end-holder.stl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]
2020-08-22 Completed setup of Microstepping. Reassinged pins per Circuit Baord
2020-08-22 Steppers off on startup. Updated readme.
2020-08-22 Updated board schematic
2020-08-23 Added Fusion360/Eagle Schematic. Updated readme.
    [ESP-32_Stepper_Hat_v6.sch]
2020-09-27 Fixed WiFi connection to work with hidden SSIDs. Generalised connection details.
    [AC_Vent.ino]
2025-05-29 Removed EEPROM state saving in favour of simply checking endstop status on init
2026-01-27 Created seperate config file + Fixed crashes, WiFi disconnects and timeouts.
    [AC_Vent.ino, config_sample.h]
2026-04-13 Rafactor including plenty of bugfixes.
    [AC_Vent.ino, config_sample.h]
2026-05-31 Added PCB schematic of current version (v2)
    [Circuit Board V2-B_Cu.gbl, Circuit Board V2-B_Mask.gbs, Circuit Board V2-B_Paste.gbp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]
